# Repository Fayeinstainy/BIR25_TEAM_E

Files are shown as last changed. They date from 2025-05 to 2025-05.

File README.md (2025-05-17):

# Smart Swarmica - A Swarm Ant Robots Project
## Overview
This project is part of a biologically-inspired swarm robot system, where multiple robots cooperate to perform tasks such as locating a wireless charger and coordinating actions using IR signals.
All circuities were **initially developed and tested on a Raspberry Pi Pico**, and later **finalized on a custom PCB using RP2035 microcontroller chip** for integration into the final robot design.
The video for the whole development process and final demonstration can be found via this link: https://www.youtube.com/watch?v=agExd-AKbOk 

## Hardware Component 

- **IR LED**: IR333
- **IR Receiver**: TSOP38238
- **Microcontroller**: RP2350-based Raspberry Pi Pico 2W
  
- **Other**: Resistors, Transistors (for LED driving), 38kHz signal source (via PWM)

## System Architecture
final_robot_sys_architecture

## Power System Architecture (Normal Operation Mode)
new_robot_power_architecture

## Software Architecture
Software_algorithm drawio-2
## Motor Control
## Navigation
## Infrared Communication
- Uses **modulated IR signals** at 38kHz for one-way signaling between robots.
- Encodes simple messages (e.g. "Relative location is (4, 12)", "Stop Moving").
- Receiver uses TSOP382 to detect incoming signals reliably even in ambient light.

### How it works:
1. IR LED emits 38kHz modulated pulses.
2. TSOP382 detects signal and triggers logic in firmware.
3. Signal interpreted as communication or wall proximity.

## PCB Design
Designed using kiCAD 9.0, project files, schematic and PCB pdfs under bio_robots/ folder, featuring the following features:
- Populated: Common anode RGB LED, 3-pairs of IR transmitters and receivers, full bridge rectifier, parallel chargers for the supercapacitors, OR controller.
- Unpopulated: ICM-20948, 1.8V regulator, level shifters, bypass strategy (U12, D10-D13)

## Obstacle Avoidance
- Based on detecting reflection of IR signal from nearby obstacles.
- If TSOP382 receives the robot’s own IR pulses reflected from a wall, it triggers a "wall detected" event.
##  WI-FI Programming Mode

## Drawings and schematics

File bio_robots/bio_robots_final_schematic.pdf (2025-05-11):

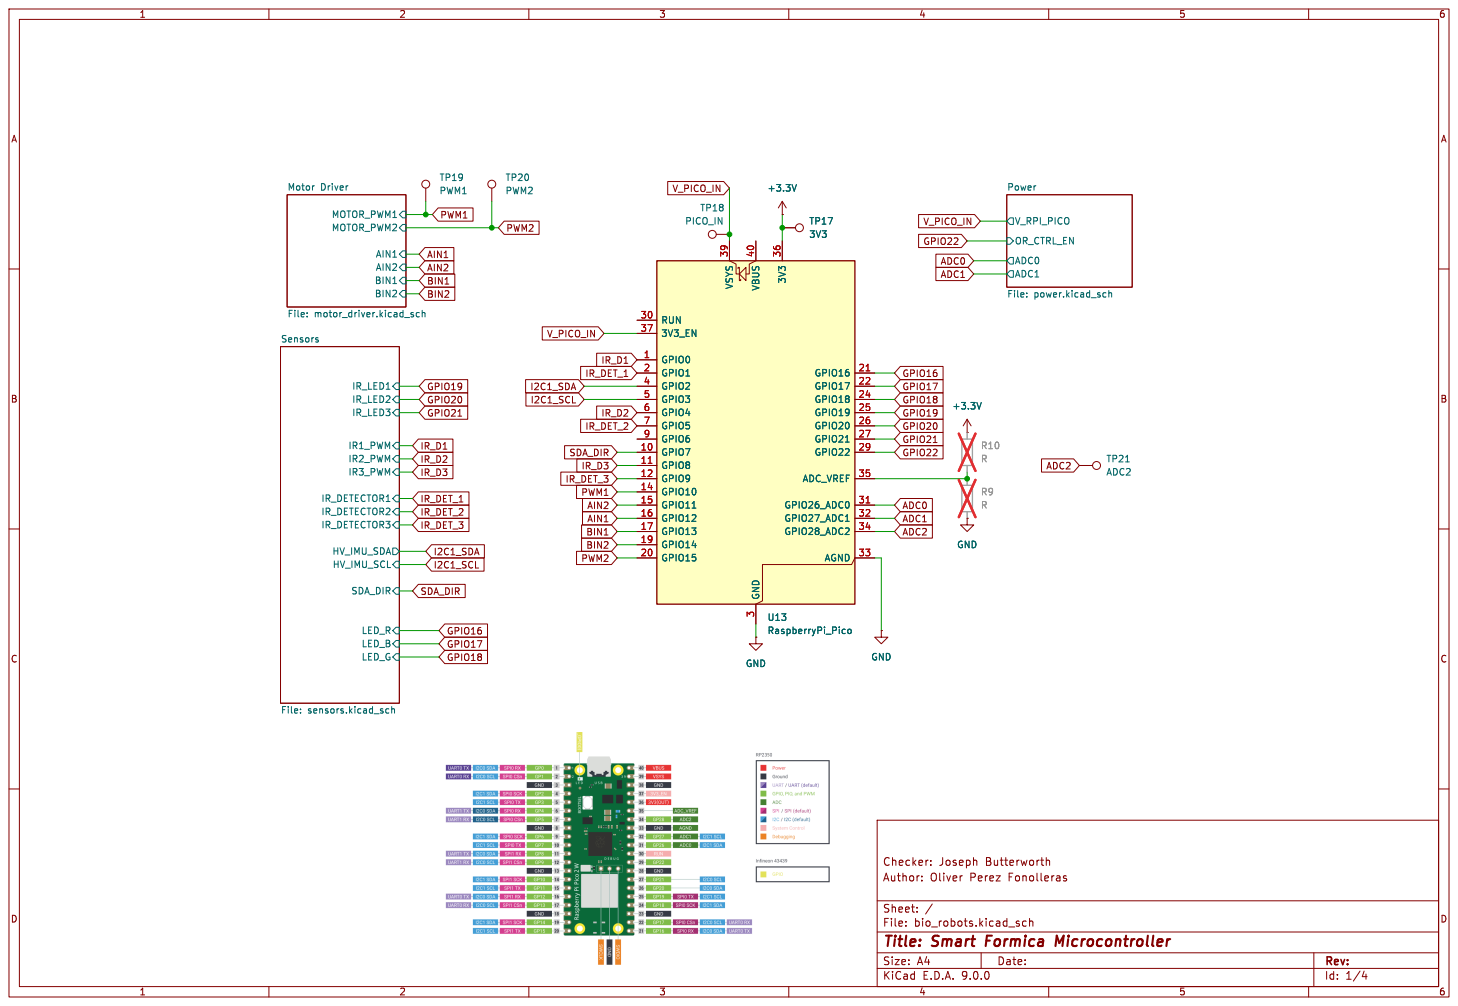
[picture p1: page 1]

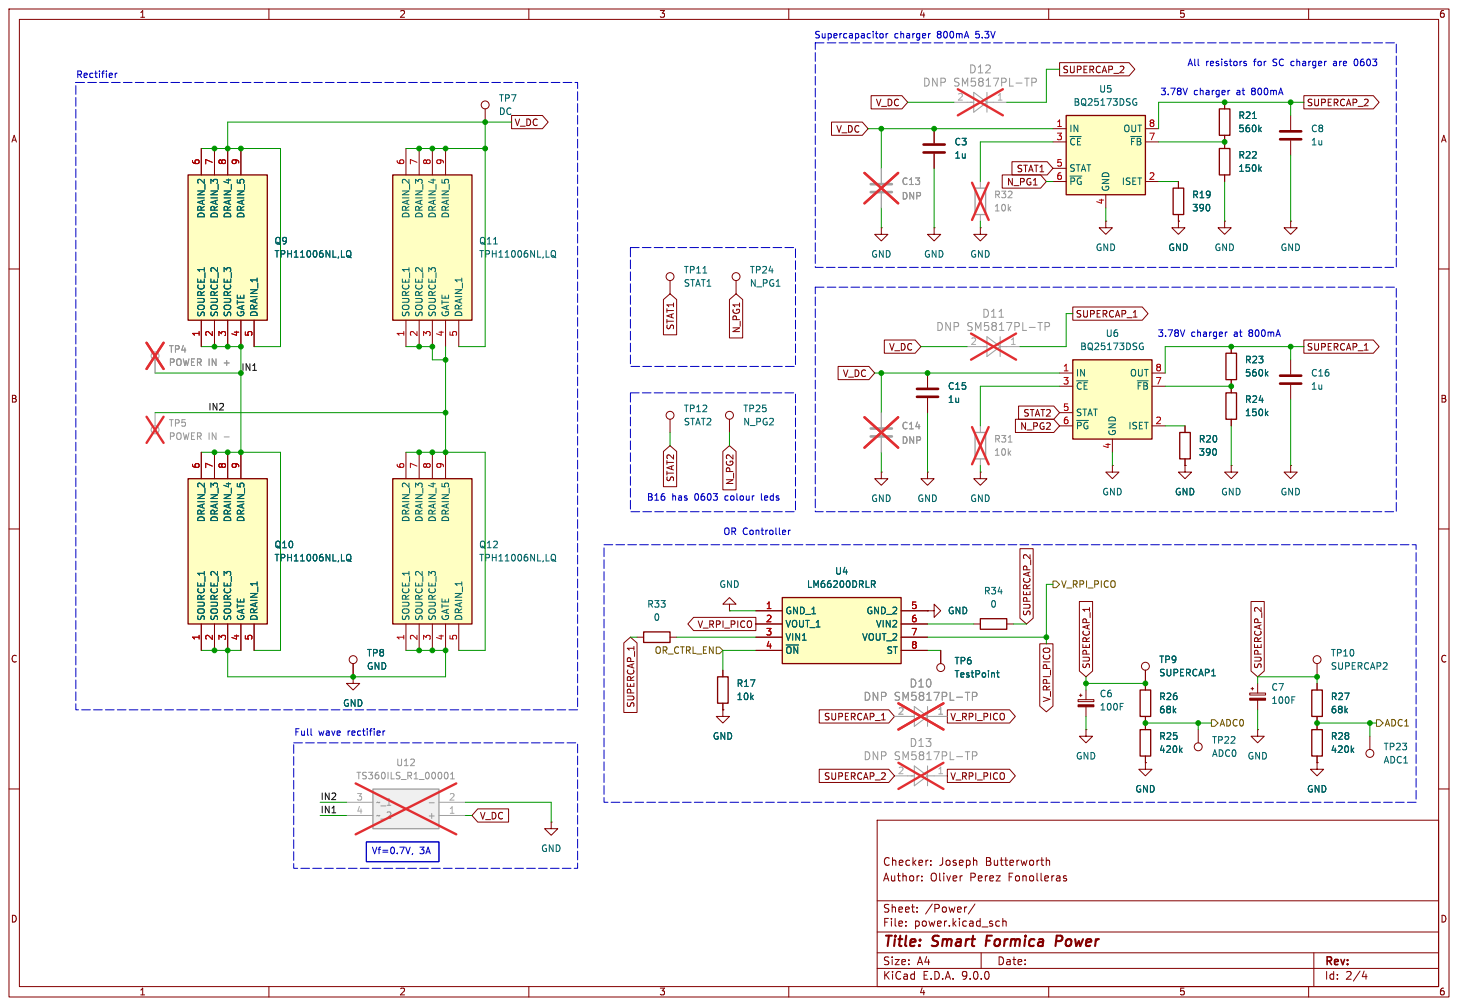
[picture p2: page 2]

6 DRAIN_3
TP5 POWER IN - TP4 POWER IN + SOURCE_1

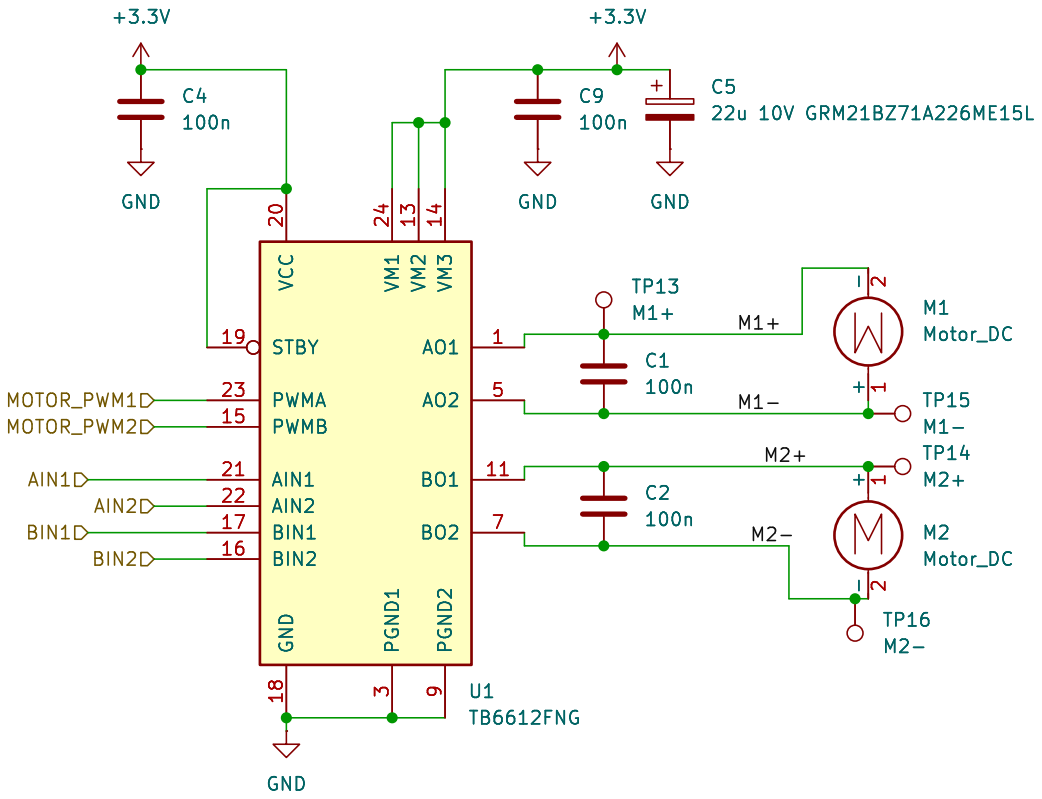
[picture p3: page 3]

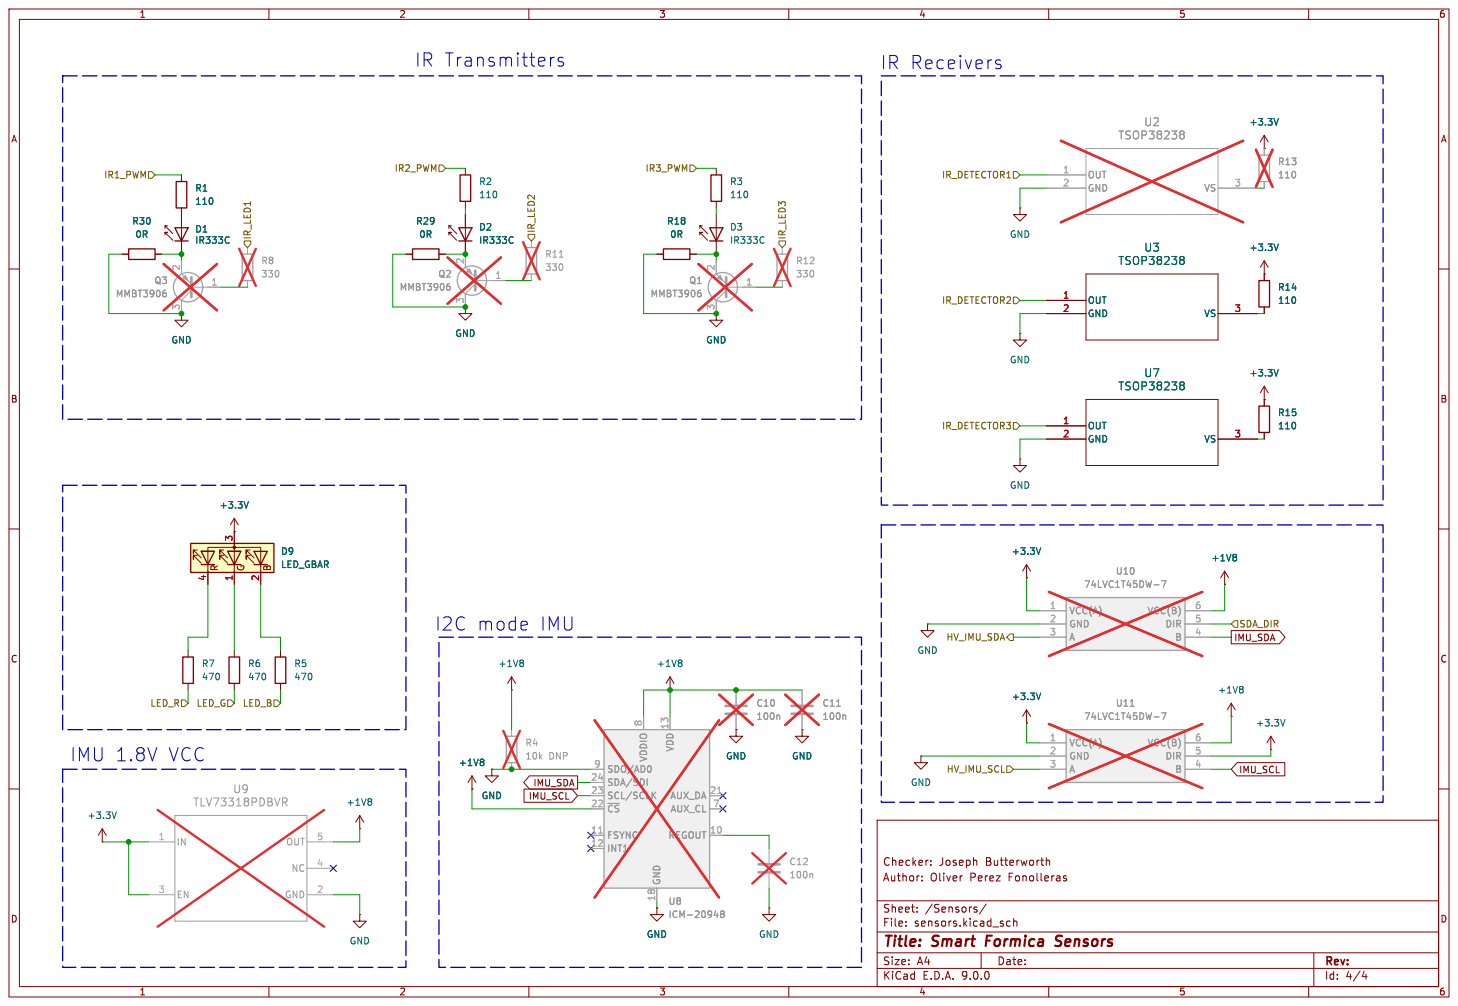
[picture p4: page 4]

Id: 4/4 Title: Smart Formica Sensors

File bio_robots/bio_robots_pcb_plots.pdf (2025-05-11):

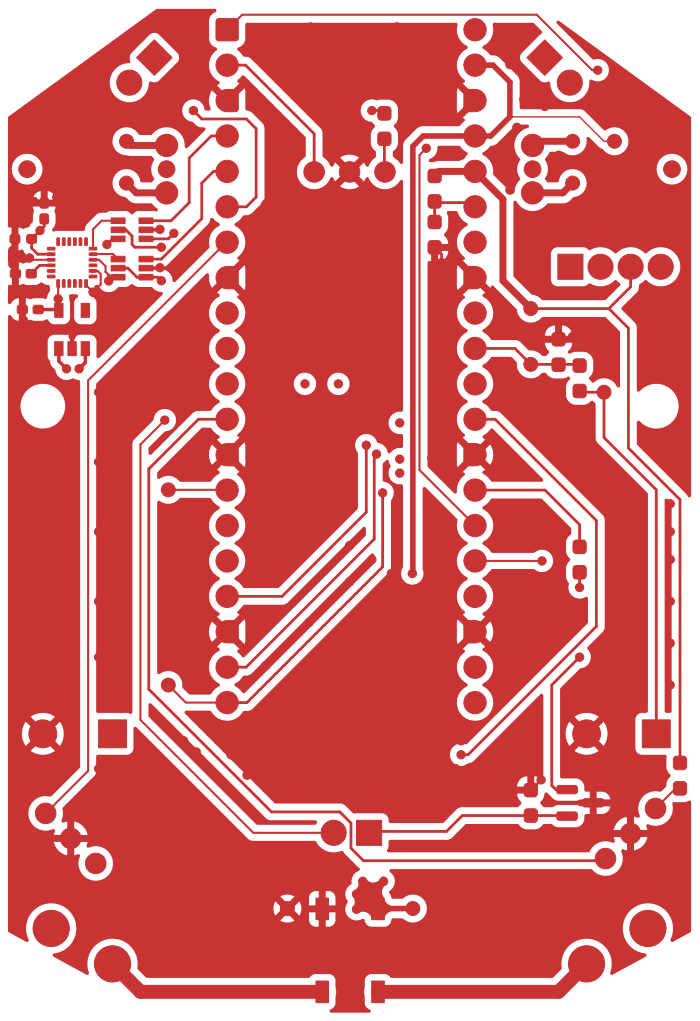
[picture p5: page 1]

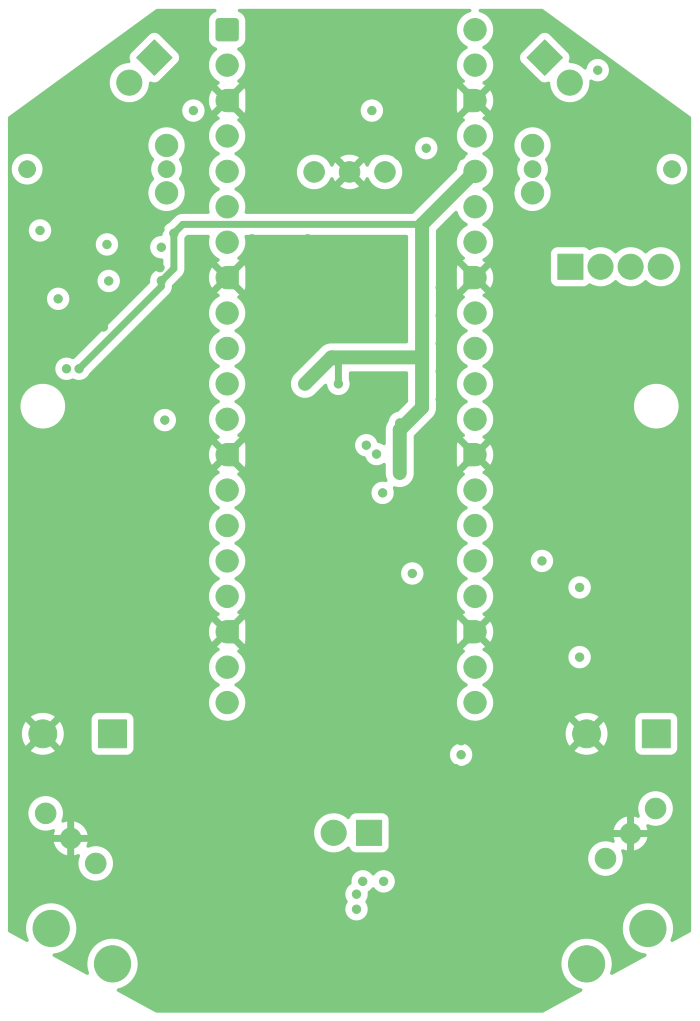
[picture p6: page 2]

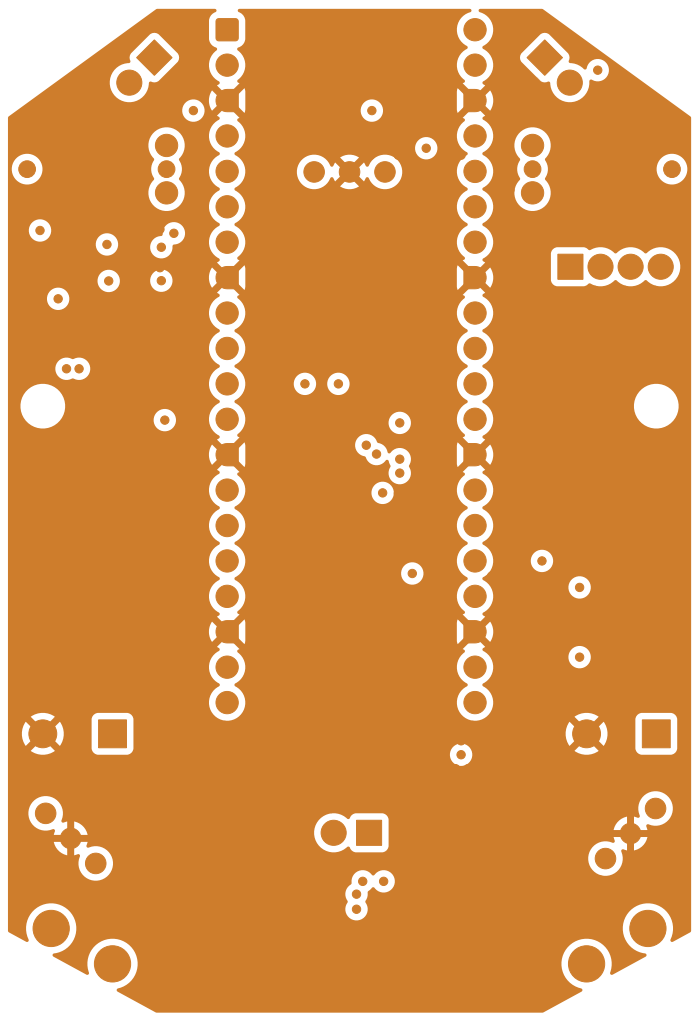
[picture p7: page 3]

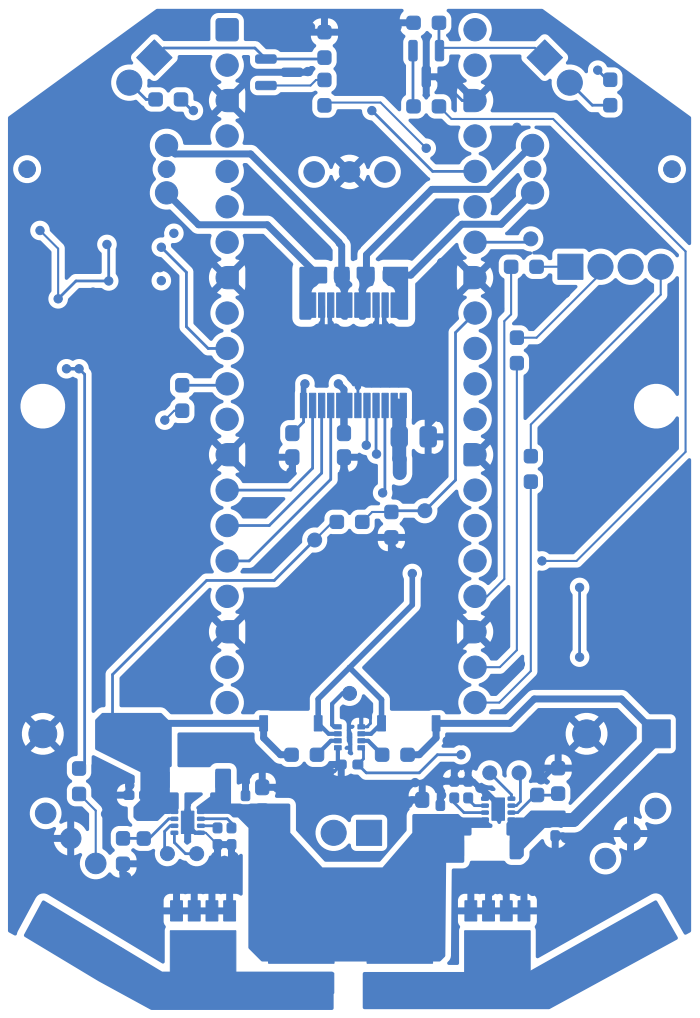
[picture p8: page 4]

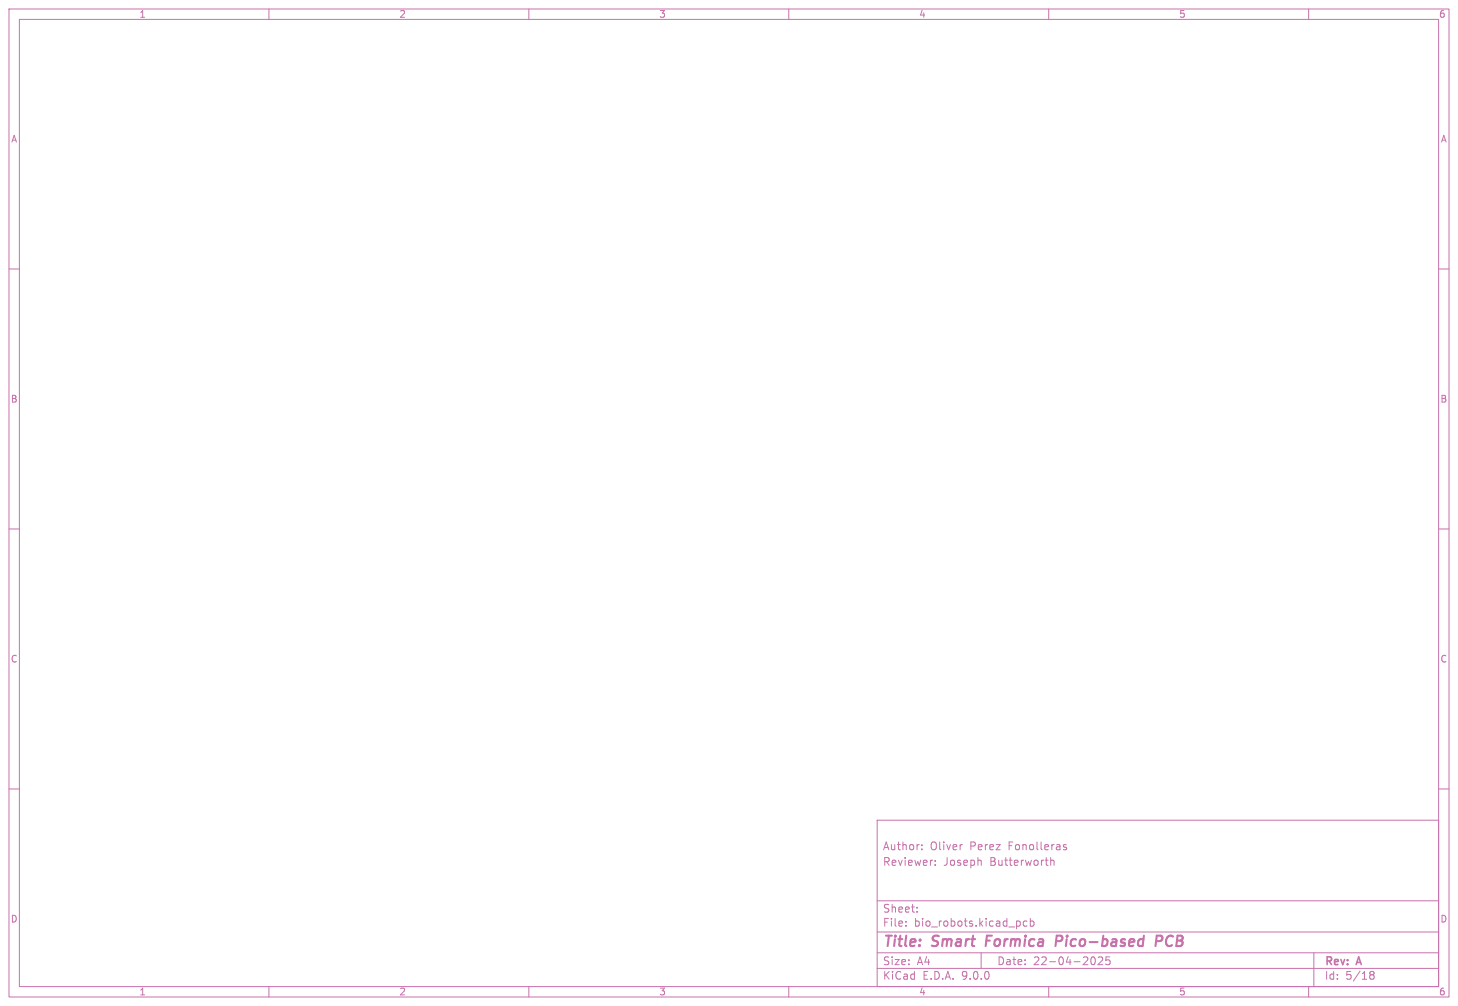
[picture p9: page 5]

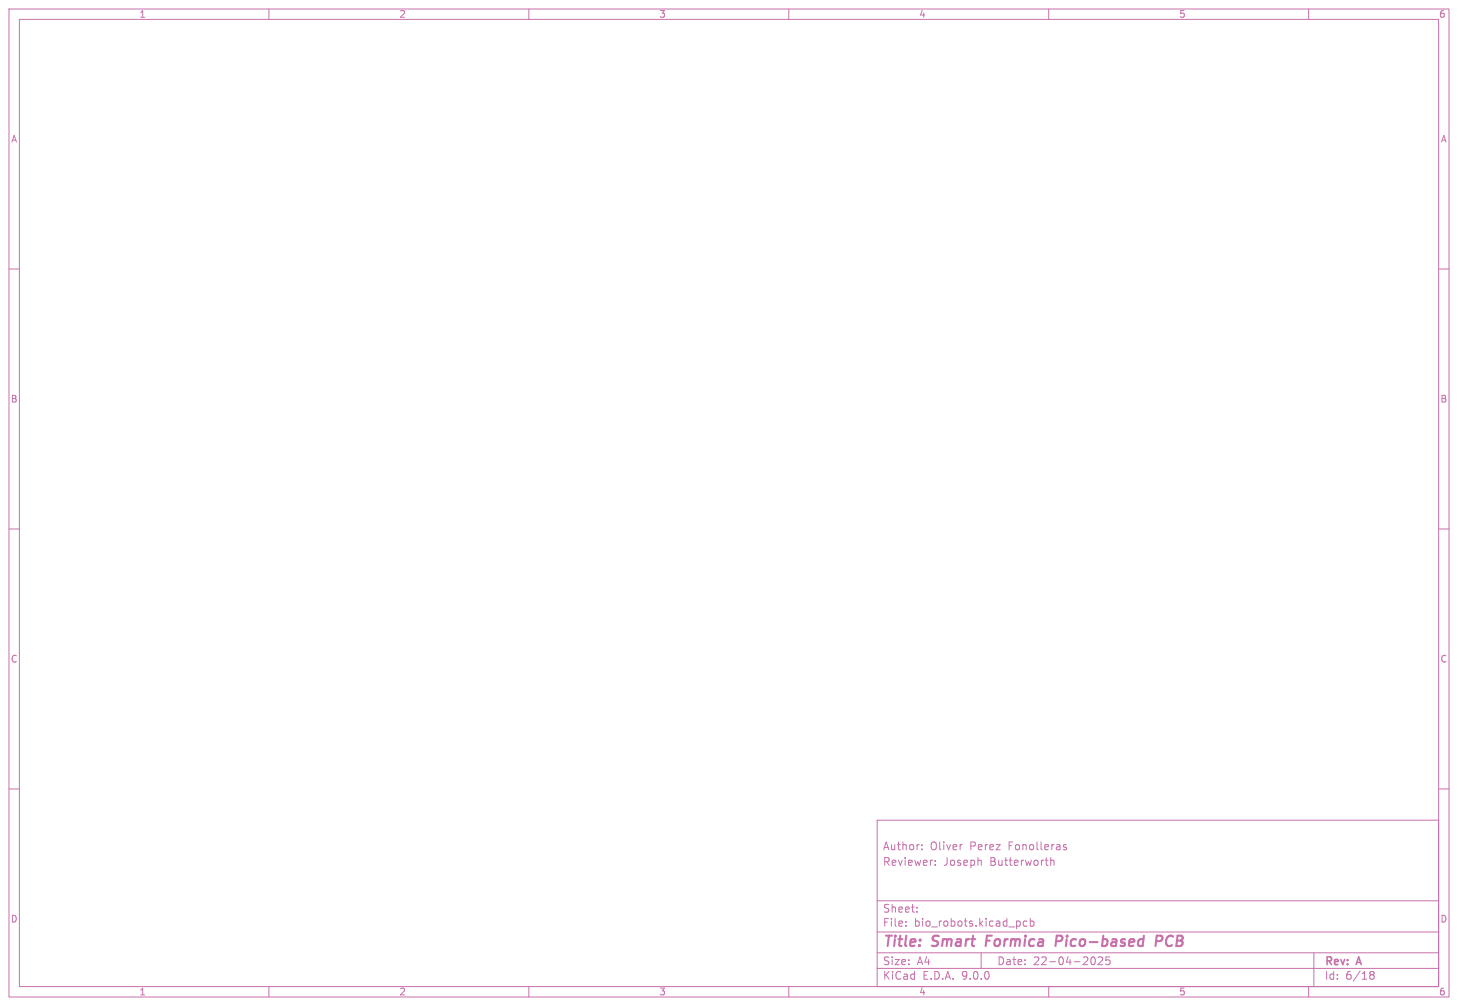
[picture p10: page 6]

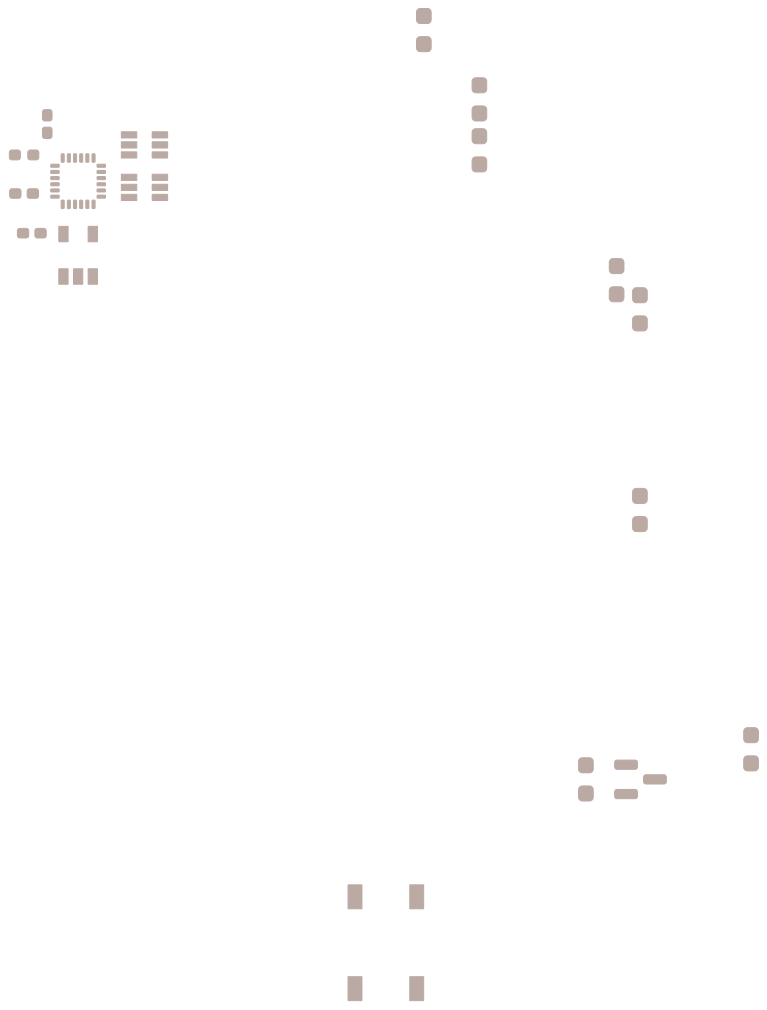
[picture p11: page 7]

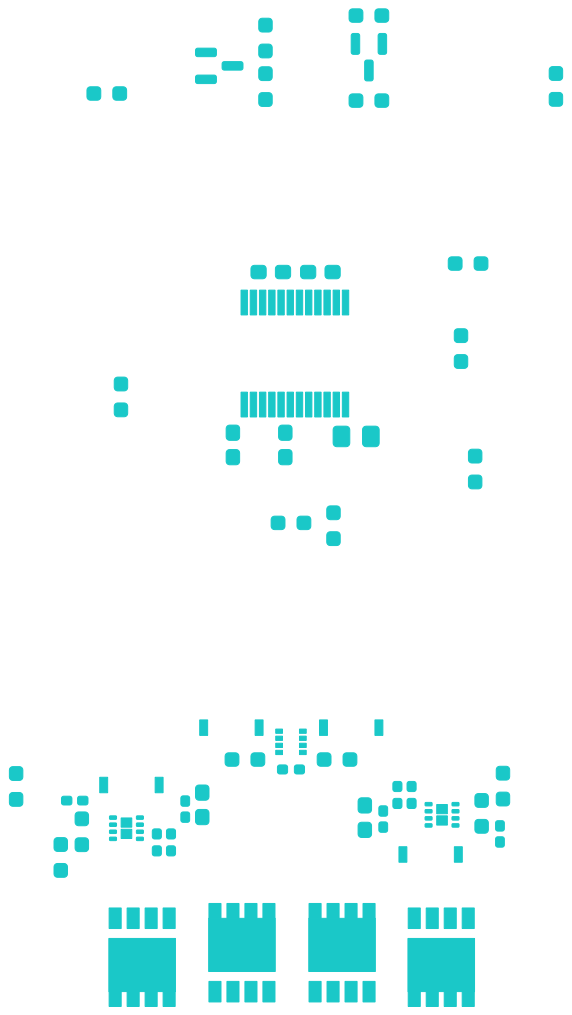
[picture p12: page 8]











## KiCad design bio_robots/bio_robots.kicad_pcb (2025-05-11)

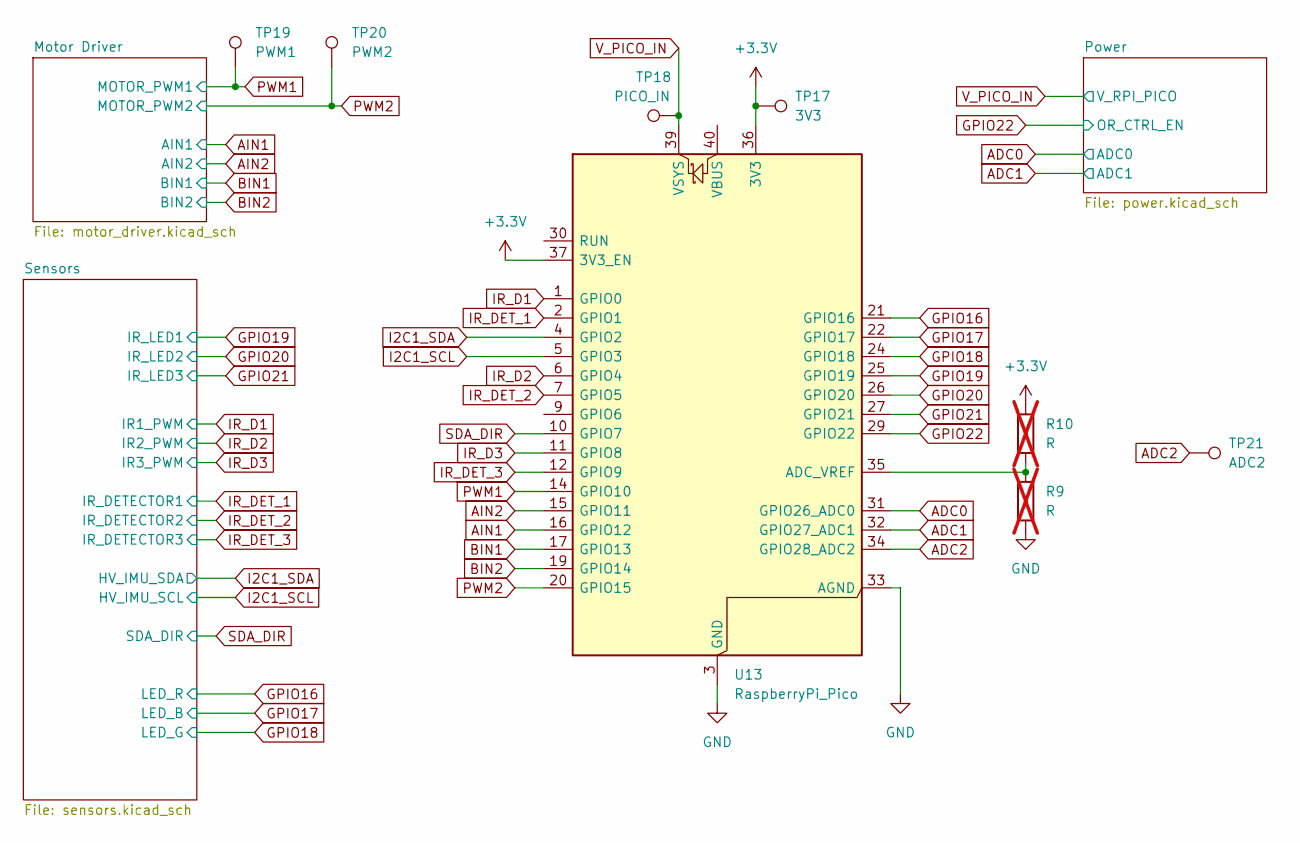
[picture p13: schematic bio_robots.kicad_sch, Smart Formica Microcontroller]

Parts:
R9, R10: R; R_0603_1608Metric_Pad0.98x0.95mm_HandSolder; not fitted
TP17: 3V3; TestPoint_Pad_D1.0mm
TP18: PICO_IN; TestPoint_Pad_D1.0mm
TP19: PWM1; TestPoint_Pad_D1.0mm
TP20: PWM2; TestPoint_Pad_D1.0mm
TP21: ADC2; TestPoint_Pad_D1.0mm
U13: RaspberryPi_Pico; mod_RaspberryPi_Pico_Common_THT

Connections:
ADC0: U13.31 (GPIO26_ADC0); also elsewhere on the board
ADC1: U13.32 (GPIO27_ADC1); also elsewhere on the board
ADC2: TP21.1, U13.34 (GPIO28_ADC2)
AIN1: U13.16 (GPIO12); also elsewhere on the board
AIN2: U13.15 (GPIO11); also elsewhere on the board
BIN1: U13.17 (GPIO13); also elsewhere on the board
BIN2: U13.19 (GPIO14); also elsewhere on the board
GND: R9.2, U13.3 (GND), U13.8 (GND), U13.13 (GND), U13.18 (GND), U13.23 (GND), U13.28 (GND), U13.33 (AGND), U13.38 (GND); also elsewhere on the board
GPIO16: U13.21 (GPIO16); also elsewhere on the board
GPIO17: U13.22 (GPIO17); also elsewhere on the board
GPIO18: U13.24 (GPIO18); also elsewhere on the board
GPIO19: U13.25 (GPIO19); also elsewhere on the board
GPIO20: U13.26 (GPIO20); also elsewhere on the board
GPIO21: U13.27 (GPIO21); also elsewhere on the board
GPIO22: U13.29 (GPIO22); also elsewhere on the board
I2C1_SCL: U13.5 (GPIO3); also elsewhere on the board
I2C1_SDA: U13.4 (GPIO2); also elsewhere on the board
IR_D1: U13.1 (GPIO0); also elsewhere on the board
IR_D2: U13.6 (GPIO4); also elsewhere on the board
IR_D3: U13.11 (GPIO8); also elsewhere on the board
IR_DET_1: U13.2 (GPIO1); also elsewhere on the board
IR_DET_2: U13.7 (GPIO5); also elsewhere on the board
IR_DET_3: U13.12 (GPIO9); also elsewhere on the board
unnamed: R9.1, R10.2, U13.35 (ADC_VREF)
PWM1: TP19.1, U13.14 (GPIO10); also elsewhere on the board
PWM2: TP20.1, U13.20 (GPIO15); also elsewhere on the board
SDA_DIR: U13.10 (GPIO7); also elsewhere on the board

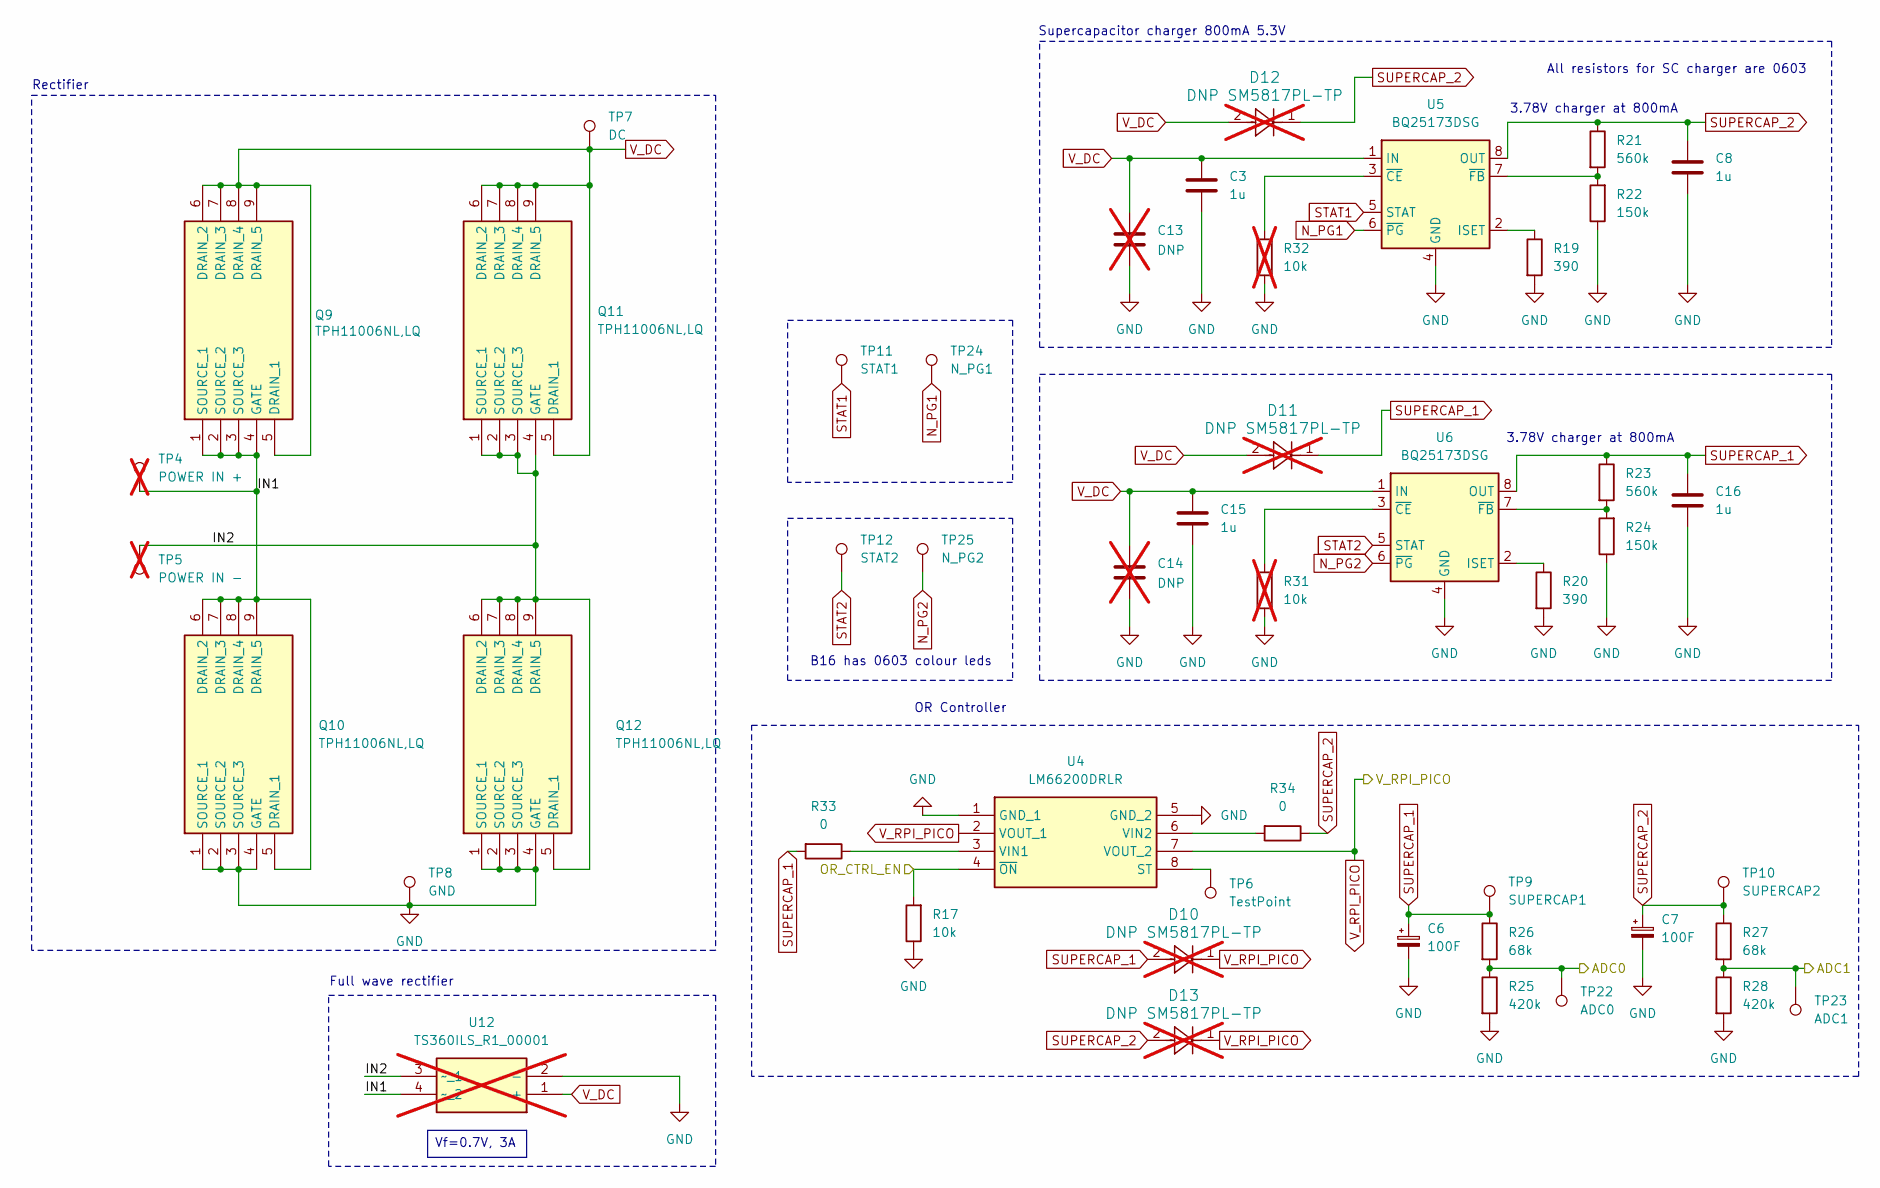
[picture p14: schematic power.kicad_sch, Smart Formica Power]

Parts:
C3, C8, C15, C16: 1u; C_0402_1005Metric_Pad0.74x0.62mm_HandSolder
C6, C7: 100F; 100f_CPhorizontal_Radial_D10.0mm_P5.00mm
C13, C14: DNP; C_0603_1608Metric_Pad1.08x0.95mm_HandSolder; not fitted
D10, D11, D12, D13: DNP SM5817PL-TP; CR_5817PL-TP_MCC-M; not fitted
Q9, Q10, Q11, Q12: TPH11006NL,LQ; TPH11006NLLQ; Mouser Part Number 757-TPH11006NLLQ
R17: 10k; R_0402_1005Metric_Pad0.72x0.64mm_HandSolder
R19, R20: 390; R_0402_1005Metric_Pad0.72x0.64mm_HandSolder
R21, R23: 560k; R_0603_1608Metric_Pad0.98x0.95mm_HandSolder
R22, R24: 150k; R_0603_1608Metric_Pad0.98x0.95mm_HandSolder
R25, R28: 420k; R_0603_1608Metric_Pad0.98x0.95mm_HandSolder
R26, R27: 68k; R_0603_1608Metric_Pad0.98x0.95mm_HandSolder
R31, R32: 10k; R_0402_1005Metric_Pad0.72x0.64mm_HandSolder; not fitted
R33, R34: 0; R_0603_1608Metric_Pad0.98x0.95mm_HandSolder
TP4: POWER IN +; TestPoint_Bridge_Pitch5.08mm_Drill1.3mm; not fitted
TP5: POWER IN -; TestPoint_Bridge_Pitch5.08mm_Drill1.3mm; not fitted
TP6: TestPoint; TestPoint_Pad_D1.0mm
TP7: DC; TestPoint_Pad_D1.0mm
TP8: GND; TestPoint_Pad_D1.0mm
TP9: SUPERCAP1; TestPoint_Pad_D1.0mm
TP10: SUPERCAP2; TestPoint_Pad_D1.0mm
TP11: STAT1; TestPoint_Pad_D1.0mm
TP12: STAT2; TestPoint_Pad_D1.0mm
TP22: ADC0; TestPoint_Pad_D1.0mm
TP23: ADC1; TestPoint_Pad_D1.0mm
TP24: N_PG1; TestPoint_Pad_D1.0mm
TP25: N_PG2; TestPoint_Pad_D1.0mm
U4: LM66200DRLR; SOTFL50P160X60-8N; Mouser Part Number 595-LM66200DRLR
U5, U6: BQ25173DSG; WSON-8-1EP_2x2mm_P0.5mm_EP0.9x1.6mm
U12: TS360ILS_R1_00001; SOP400P650X145-4N; Mouser Part Number 241-TS360ILSR100001; not fitted

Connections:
/Power/IN1: Q9.1 (SOURCE_1), Q9.2 (SOURCE_2), Q9.3 (SOURCE_3), Q9.4 (GATE), Q10.5 (DRAIN_1), Q10.6 (DRAIN_2), Q10.7 (DRAIN_3), Q10.8 (DRAIN_4), Q10.9 (DRAIN_5), TP4.1, U12.4 (~_2)
/Power/IN2: Q11.1 (SOURCE_1), Q11.2 (SOURCE_2), Q11.3 (SOURCE_3), Q11.4 (GATE), Q12.5 (DRAIN_1), Q12.6 (DRAIN_2), Q12.7 (DRAIN_3), Q12.8 (DRAIN_4), Q12.9 (DRAIN_5), TP5.1, U12.3 (~_1)
ADC0: R25.1, R26.2, TP22.1; also elsewhere on the board
ADC1: R27.2, R28.1, TP23.1; also elsewhere on the board
GND: C3.2, C6.2, C7.2, C8.2, C13.2, C14.2, C15.2, C16.2, Q10.1 (SOURCE_1), Q10.2 (SOURCE_2), Q10.3 (SOURCE_3), Q10.4 (GATE), Q12.1 (SOURCE_1), Q12.2 (SOURCE_2), Q12.3 (SOURCE_3), Q12.4 (GATE), R17.1, R19.2, R20.2, R22.1, R24.1, R25.2, R28.2, R31.1, R32.1, TP8.1, U4.1 (GND_1), U4.5 (GND_2), U5.4 (GND), U5.9 (GND), U6.4 (GND), U6.9 (GND), U12.2 (-); also elsewhere on the board
GPIO22: R17.2, U4.4 (~ON); also elsewhere on the board
N_PG1: TP24.1, U5.6 (~PG)
N_PG2: TP25.1, U6.6 (~PG)
unnamed: TP6.1, U4.8 (ST)
unnamed: R33.1, U4.3 (VIN1)
unnamed: R34.2, U4.6 (VIN2)
unnamed: R19.1, U5.2 (ISET)
unnamed: R32.2, U5.3 (~CE)
unnamed: R21.2, R22.2, U5.7 (~FB)
unnamed: R20.1, U6.2 (ISET)
unnamed: R31.2, U6.3 (~CE)
unnamed: R23.2, R24.2, U6.7 (~FB)
STAT1: TP11.1, U5.5 (STAT)
STAT2: TP12.1, U6.5 (STAT)
SUPERCAP_1: C6.1, C16.1, D10.2, D11.1, R23.1, R26.1, R33.2, TP9.1, U6.8 (OUT)
SUPERCAP_2: C7.1, C8.1, D12.1, D13.2, R21.1, R27.1, R34.1, TP10.1, U5.8 (OUT)
V_DC: C3.1, C13.1, C14.1, C15.1, D11.2, D12.2, Q9.5 (DRAIN_1), Q9.6 (DRAIN_2), Q9.7 (DRAIN_3), Q9.8 (DRAIN_4), Q9.9 (DRAIN_5), Q11.5 (DRAIN_1), Q11.6 (DRAIN_2), Q11.7 (DRAIN_3), Q11.8 (DRAIN_4), Q11.9 (DRAIN_5), TP7.1, U5.1 (IN), U6.1 (IN), U12.1 (+)

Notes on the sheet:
Rectifier
3.78V charger at 800mA
Supercapacitor charger 800mA 5.3V
OR Controller
All resistors for SC charger are 0603
B16 has 0603 colour leds
Full wave rectifier
Vf=0.7V, 3A

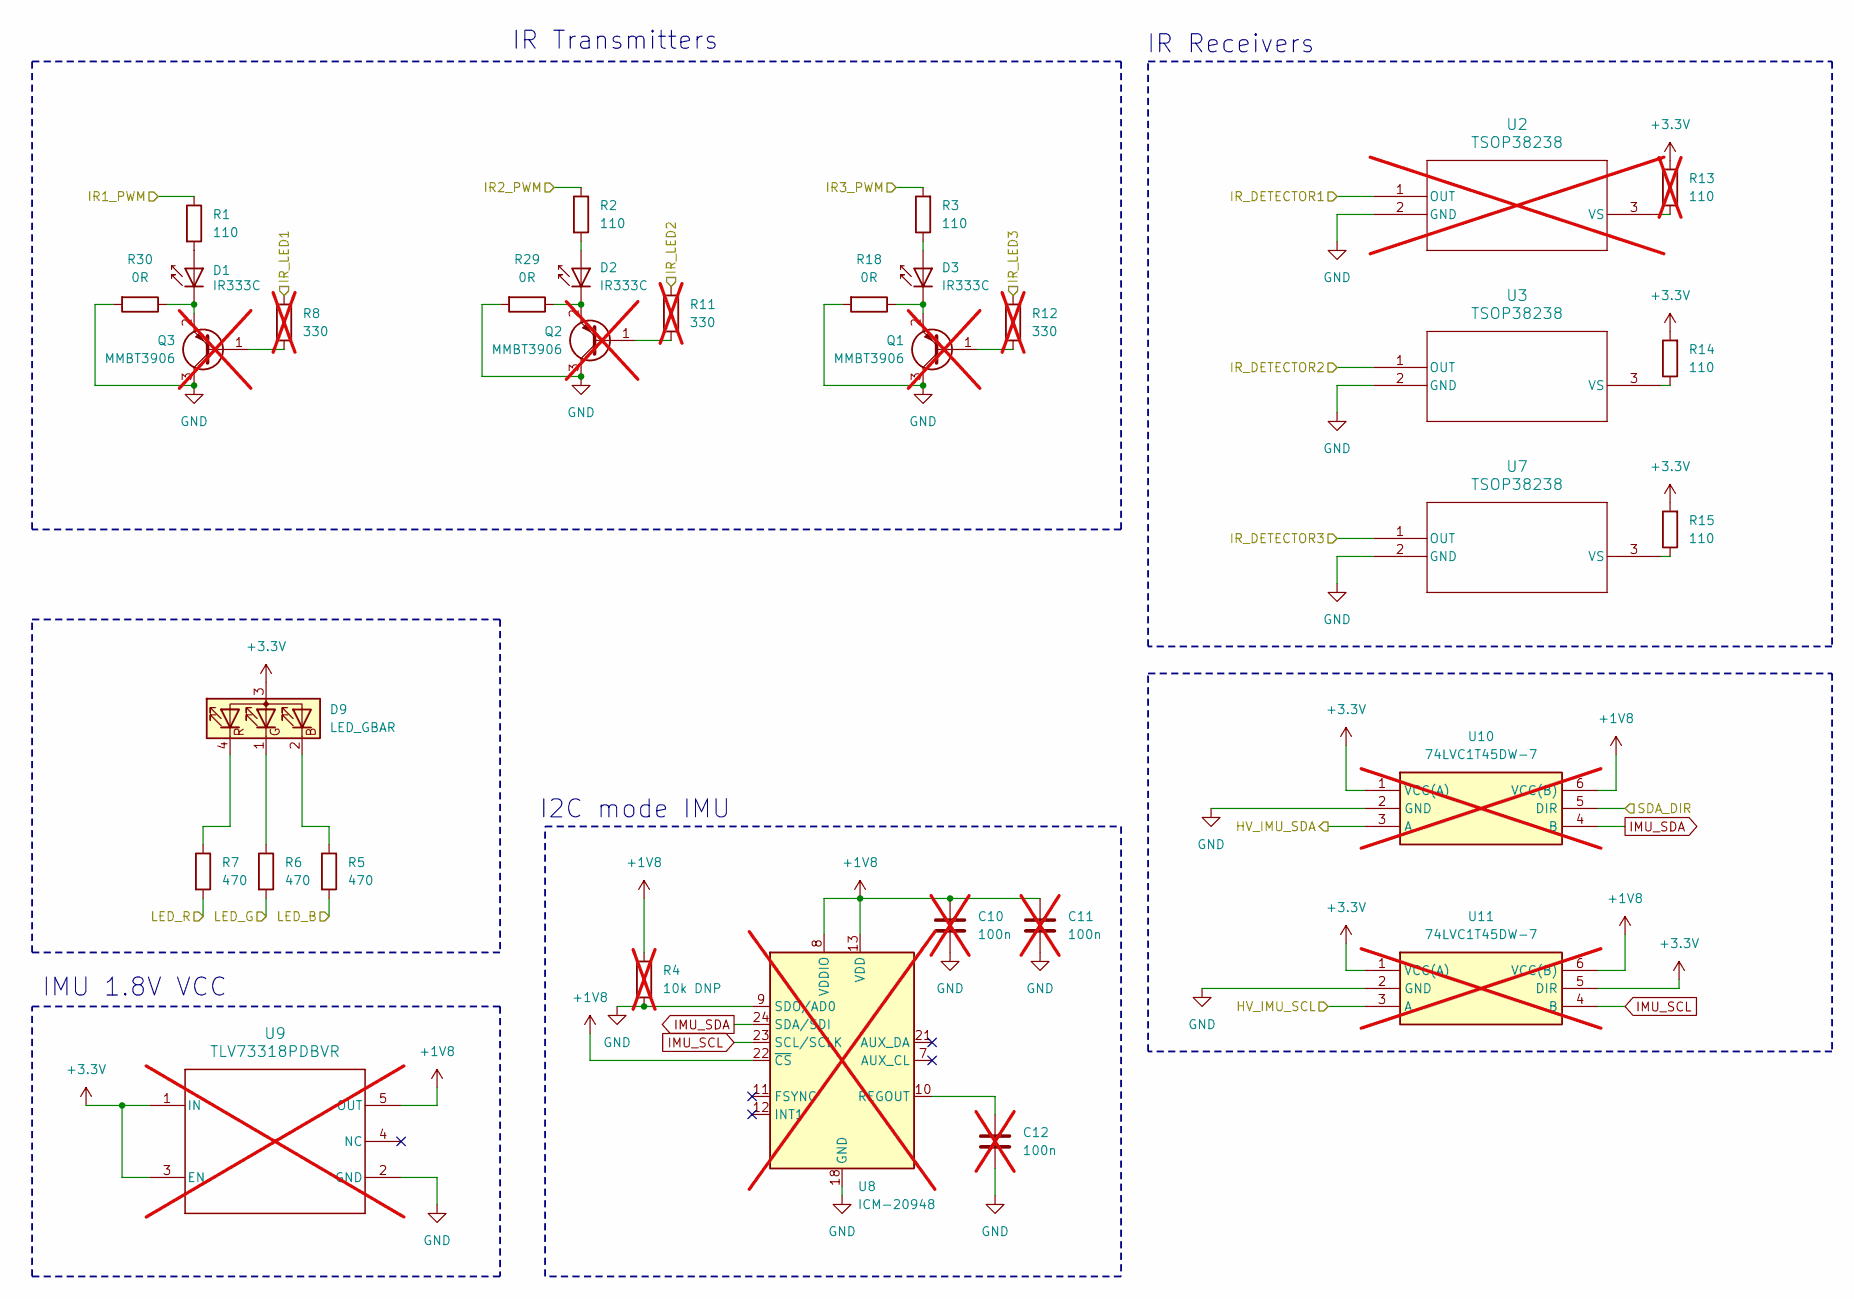
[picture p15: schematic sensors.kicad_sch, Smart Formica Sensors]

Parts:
C10, C11, C12: 100n; C_0402_1005Metric_Pad0.74x0.62mm_HandSolder; not fitted
D1, D2, D3: IR333C; LED_D5.0mm_IRGrey
D9: LED_GBAR; LED_D5.0mm-4_RGB_Wide_Pins
Q1, Q2, Q3: MMBT3906; SOT-23; not fitted
R1, R2, R3, R14, R15: 110; R_0603_1608Metric_Pad0.98x0.95mm_HandSolder
R4: 10k DNP; R_0402_1005Metric_Pad0.72x0.64mm_HandSolder; not fitted
R5, R6, R7: 470; R_0603_1608Metric_Pad0.98x0.95mm_HandSolder
R8, R11, R12: 330; R_0603_1608Metric_Pad0.98x0.95mm_HandSolder; not fitted
R13: 110; R_0603_1608Metric_Pad0.98x0.95mm_HandSolder; not fitted
R18, R29, R30: 0R; R_0603_1608Metric_Pad0.98x0.95mm_HandSolder
U2: TSOP38238; not fitted
U3, U7: TSOP38238
U8: ICM-20948; InvenSense_QFN-24_3x3mm_P0.4mm; not fitted
U9: TLV73318PDBVR; DBV0005A_N; not fitted
U10, U11: 74LVC1T45DW-7; SOT65P210X110-6N; Mouser Part Number 621-74LVC1T45DW-7; not fitted

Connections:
+1V8: C10.1, C11.1, R4.1, U8.8 (VDDIO), U8.13 (VDD), U8.22 (~CS), U9.5 (OUT), U10.6 (VCC(B)), U11.6 (VCC(B))
GND: C10.2, C11.2, C12.2, Q1.3 (C), Q2.3 (C), Q3.3 (C), R4.2, R18.2, R29.2, R30.2, U2.2 (GND), U3.2 (GND), U7.2 (GND), U8.9 (SDO/AD0), U8.18 (GND), U8.20 (GND), U9.2 (GND), U10.2 (GND), U11.2 (GND); also elsewhere on the board
GPIO16: R7.2; also elsewhere on the board
GPIO17: R5.2; also elsewhere on the board
GPIO18: R6.2; also elsewhere on the board
GPIO19: R8.1; also elsewhere on the board
GPIO20: R11.1; also elsewhere on the board
GPIO21: R12.1; also elsewhere on the board
I2C1_SCL: U11.3 (A); also elsewhere on the board
I2C1_SDA: U10.3 (A); also elsewhere on the board
IMU_SCL: U8.23 (SCL/SCLK), U11.4 (B)
IMU_SDA: U8.24 (SDA/SDI), U10.4 (B)
IR_D1: R1.1; also elsewhere on the board
IR_D2: R2.1; also elsewhere on the board
IR_D3: R3.2; also elsewhere on the board
IR_DET_1: U2.1 (OUT); also elsewhere on the board
IR_DET_2: U3.1 (OUT); also elsewhere on the board
IR_DET_3: U7.1 (OUT); also elsewhere on the board
unnamed: D1.2 (A), R1.2
unnamed: D1.1 (K), Q3.2 (E), R30.1
unnamed: D2.2 (A), R2.2
unnamed: D2.1 (K), Q2.2 (E), R29.1
unnamed: D3.2 (A), R3.1
unnamed: D3.1 (K), Q1.2 (E), R18.1
unnamed: D9.2 (BK), R5.1
unnamed: D9.1 (GK), R6.1
unnamed: D9.4 (RK), R7.1
unnamed: Q1.1 (B), R12.2
unnamed: Q2.1 (B), R11.2
unnamed: Q3.1 (B), R8.2
unnamed: R13.1, U2.3 (VS)
unnamed: R14.1, U3.3 (VS)
unnamed: R15.1, U7.3 (VS)
unnamed: C12.1, U8.10 (REGOUT)
SDA_DIR: U10.5 (DIR); also elsewhere on the board

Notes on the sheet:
IR Receivers
IR Transmitters
I2C mode IMU
IMU 1.8V VCC

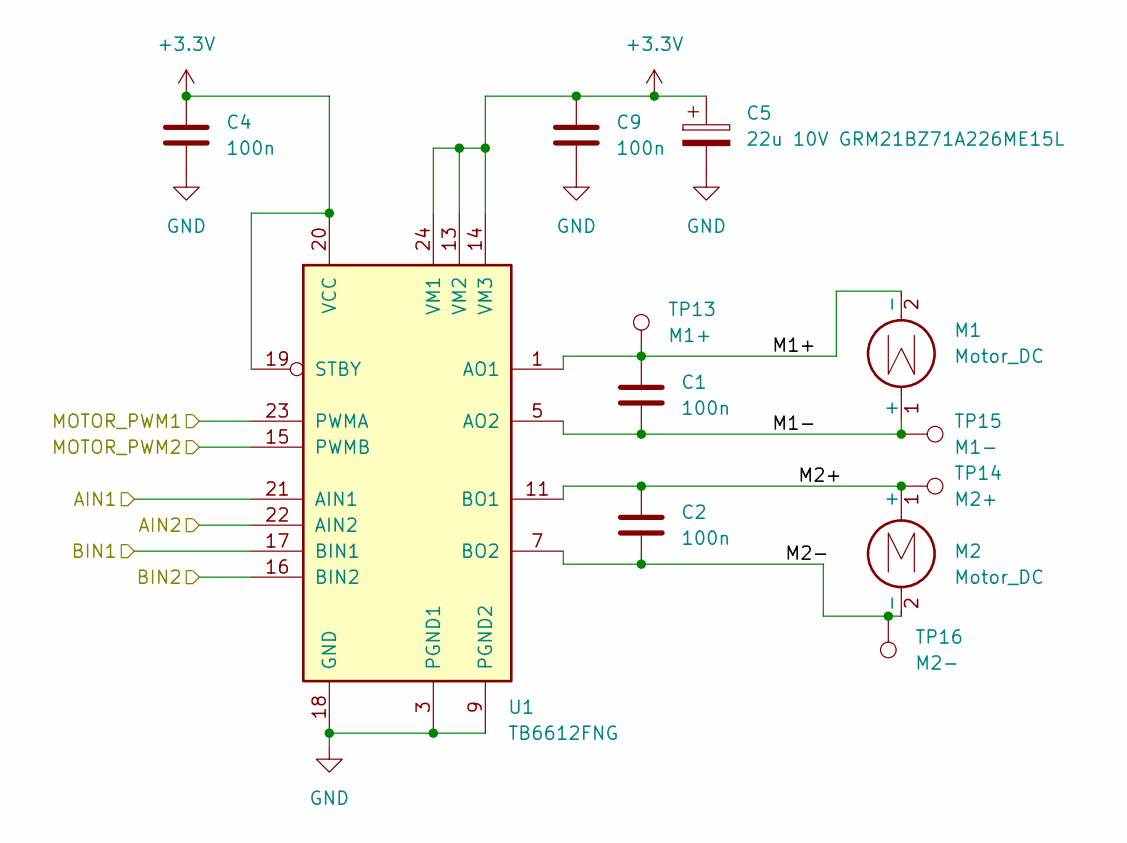
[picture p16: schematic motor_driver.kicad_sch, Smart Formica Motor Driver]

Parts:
C1, C2, C4, C9: 100n; C_0603_1608Metric_Pad1.08x0.95mm_HandSolder
C5: 22u 10V GRM21BZ71A226ME15L; C_0805_2012Metric_Pad1.18x1.45mm_HandSolder
M1, M2: Motor_DC; mod_motor_v2_VZ6SC0B0060081
TP13: M1+; TestPoint_Pad_D1.0mm
TP14: M2+; TestPoint_Pad_D1.0mm
TP15: M1-; TestPoint_Pad_D1.0mm
TP16: M2-; TestPoint_Pad_D1.0mm
U1: TB6612FNG; SSOP-24_5.3x8.2mm_P0.65mm

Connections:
/Motor Driver/M1+: C1.1, M1.2 (-), TP13.1, U1.1 (AO1), U1.2 (AO1)
/Motor Driver/M1-: C1.2, M1.1 (+), TP15.1, U1.5 (AO2), U1.6 (AO2)
/Motor Driver/M2+: C2.1, M2.1 (+), TP14.1, U1.11 (BO1), U1.12 (BO1)
/Motor Driver/M2-: C2.2, M2.2 (-), TP16.1, U1.7 (BO2), U1.8 (BO2)
AIN1: U1.21 (AIN1); also elsewhere on the board
AIN2: U1.22 (AIN2); also elsewhere on the board
BIN1: U1.17 (BIN1); also elsewhere on the board
BIN2: U1.16 (BIN2); also elsewhere on the board
GND: C4.2, C5.2, C9.2, U1.3 (PGND1), U1.4 (PGND1), U1.9 (PGND2), U1.10 (PGND2), U1.18 (GND); also elsewhere on the board
PWM1: U1.23 (PWMA); also elsewhere on the board
PWM2: U1.15 (PWMB); also elsewhere on the board

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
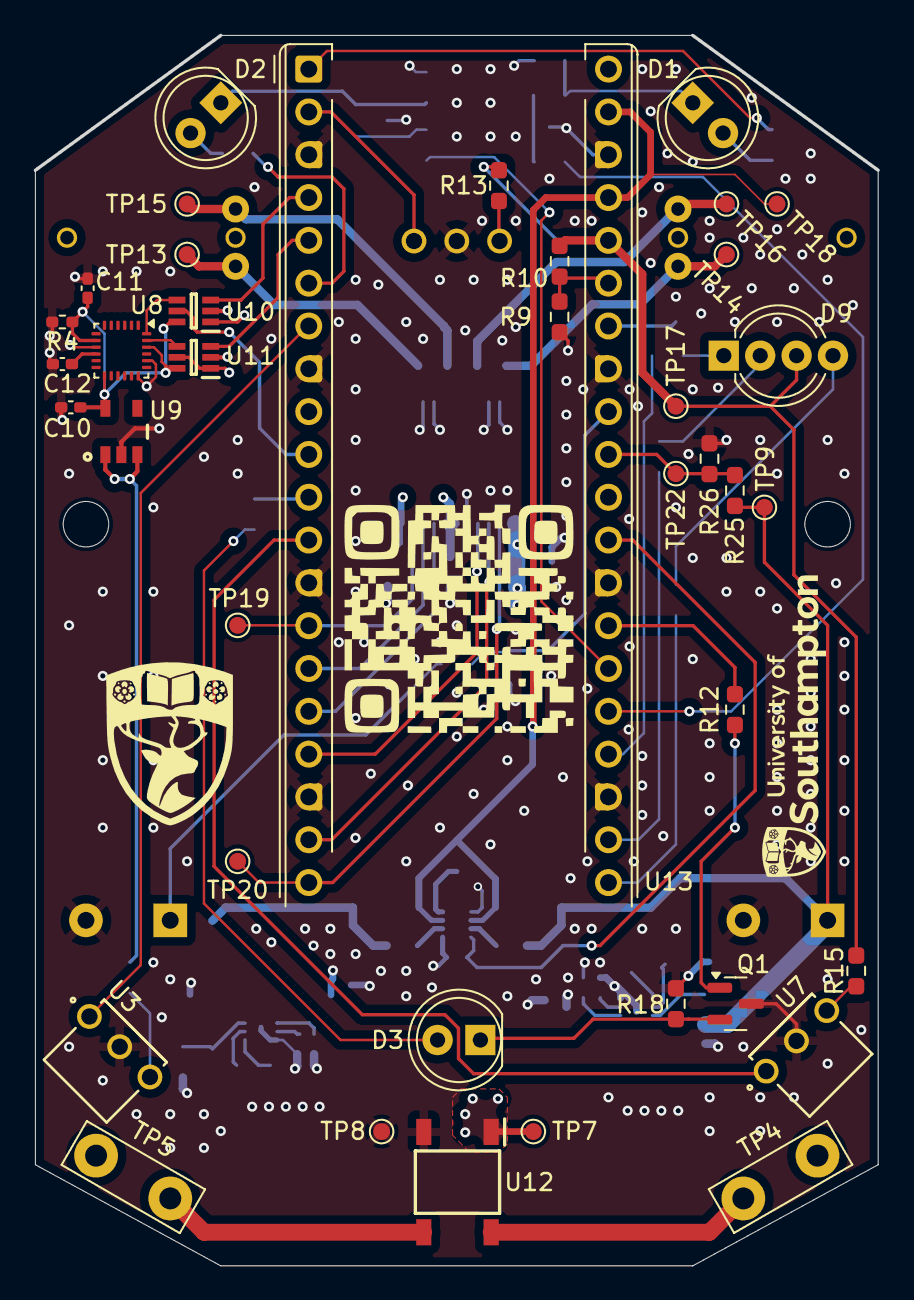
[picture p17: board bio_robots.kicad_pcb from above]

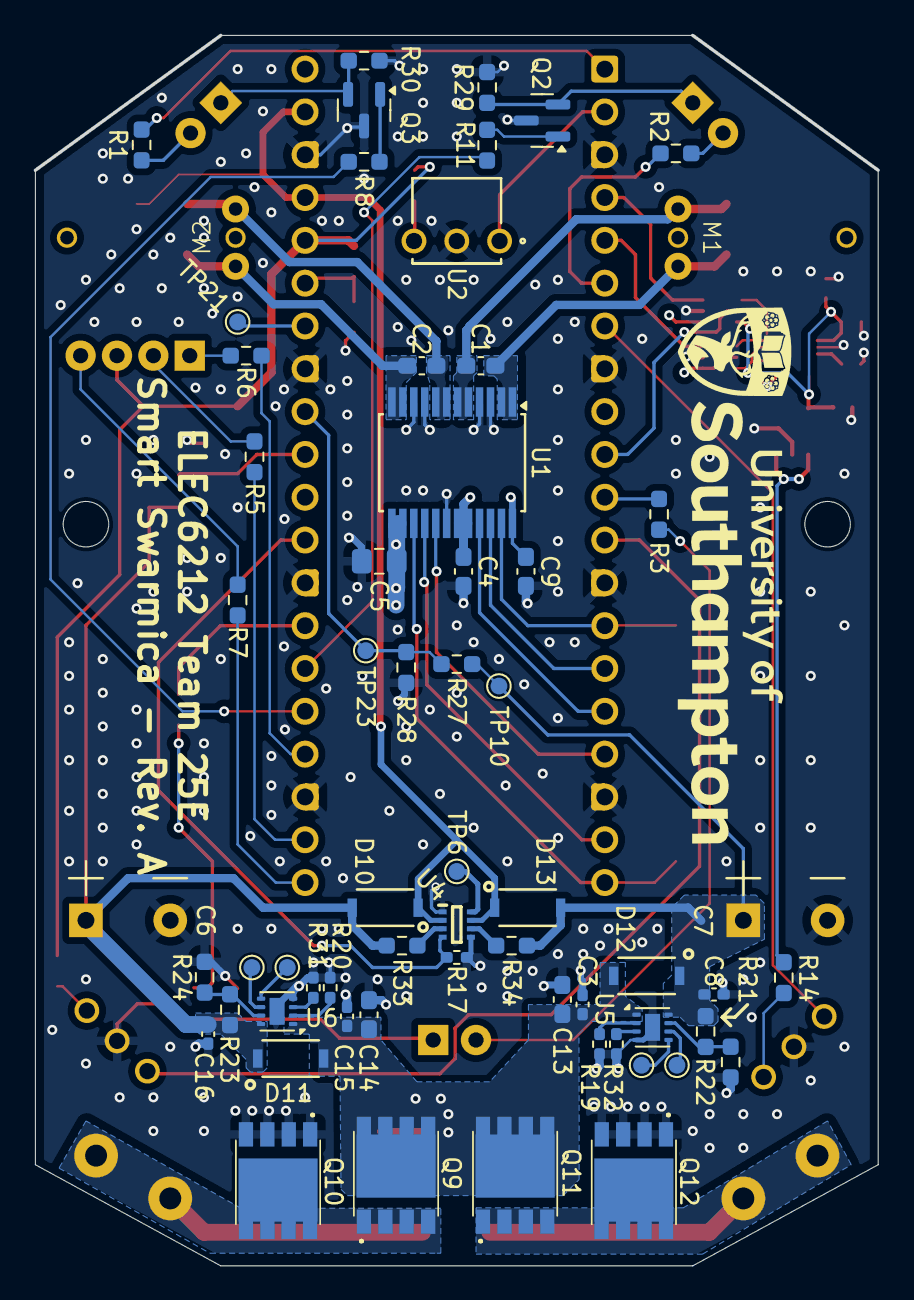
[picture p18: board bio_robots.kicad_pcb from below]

Board: 4 copper layers, 50.0 x 73.0 mm, 103 parts (62 on the bottom side), 70 nets.

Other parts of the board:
MH1, MH2: MountingHole_2.7mm_M2.5_DIN965

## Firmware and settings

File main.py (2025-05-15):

from picozero import RGBLED
from time import sleep
import math
import random
from machine import Pin , PWM
import machine
import rp2
import sys
import time
#from machine import WDT, reset
from machine import reset, WDT, Pin, PWM, reset_cause, PWRON_RESET

# if machine.reset_cause() != machine.PWRON_RESET:  # 如果不是上电复位
#     print("wrong detecting, resetting...")
#     time.sleep(1)       # 等待串口输出完成
#     machine.reset()     # 强制硬件复位

wdt = WDT(timeout=8000) #8 seconds watchdog

# --------- Setup --------- #
IR_transmitter_pin = PWM(Pin(0))
IR_transmitter_pin.freq(38000)  # 38kHz carrier
IR_transmitter_pin2 = PWM(Pin(4))
IR_transmitter_pin2.freq(38000)  # 38kHz carrier
IR_transmitter_pin3 = PWM(Pin(8))
IR_transmitter_pin3.freq(38000)  # 38kHz carrier

IR_receiver_pin1 = Pin(5, Pin.IN)
IR_receiver_pin2 = Pin(9, Pin.IN)
#1 and 9 are not working on Beth.(No Rx 1)
#1 not working on Bella (No Rx 1)
#1 not working on Cursed (No Rx 1)

rgb = RGBLED(red = 16, green = 17, blue = 18,active_high=False)

IR_transmitter_pin.duty_u16(38000)  # Enable IR signal
IR_transmitter_pin2.duty_u16(38000)  # Enable IR signal
IR_transmitter_pin3.duty_u16(38000)  # Enable IR signal

# tran1 = Pin(19, Pin.OUT)
# tran2 = Pin(20, Pin.OUT)
# tran3 = Pin(21, Pin.OUT)
# 
# tran1.value(0)
# tran2.value(0)
# tran3.value(0)
#detected = False
#--------------------walldetection----------#
def wall_detection_notworking():
    print("Wall detection started")
    #IR_transmitter_pin.duty_u16(32768)
    start = time.ticks_ms()
    
    
    while time.ticks_diff(time.ticks_ms(),start) < WALL_DETECTION_WINDOW_MS:
        if IR_receiver_pin.value()==0:
            #print("IR Signal Detected!")
            detected = True
        #elif IR_receiver_pin.value()==0:
            #print("No Signal")
    
    #IR_transmitter_pin.duty_u16(0)
    if detected == True:
        print("Wall detected")
        rgb.color = (255,0,0) #red
        sleep(1)
        #led_receiver_pin.value(1)

    else:
        print("Wall cleared!")
        rgb.color =(100,0,100) #red+green
        sleep(1)
        #led_receiver_pin.value(0)
        
# --------- Wall Detection --------- #
def wall_detection():
     
    #print("Wall detection started")
    #global detected

    time.sleep_ms(1)  # Allow some time for signal to bounce back

    if IR_receiver_pin1.value()==0 or IR_receiver_pin2.value() == 0:
        #detected = True
        print("IR Signal Detected!")
        rgb.color = (255, 0, 0) #red
        return True
    else:
        print("No Signal.")
        rgb.color = (0, 0, 255) #
        return False

#---------------------motor/navigation--------------------
#rgb = RGBLED(red = 16, green = 17, blue = 18,active_high=False) 
distance = 1.0 #polar distancce of the current location
angle = 0.0 #polar angle of the current location
direction = 0.0 #where the robot is facing
coord = [distance,angle, direction] 
turn_left = 0
turn_right = 0
turn = [turn_left, turn_right] 
count = 0
led = Pin('LED', Pin.OUT)

ain1 = Pin(12,Pin.OUT)
ain2 = Pin(11, Pin.OUT)
bin1 = Pin(13,Pin.OUT)
bin2 = Pin(14,Pin.OUT)
pwma = PWM(Pin(10))
pwmb = PWM(Pin(15))
pwma.freq(24000)
pwmb.freq(24000)

def RotateCW(duty, pwm):
    ain1.value(1)
    ain2.value(0)
    bin1.value(1)
    bin2.value(0)
    duty_16 = int(duty)
    pwm.duty_u16(duty_16)

def RotateCCW(duty, pwm):
    ain1.value(0)
    ain2.value(1)
    bin1.value(0)
    bin2.value(1)
    duty_16 = int(duty)
    pwm.duty_u16(duty_16)
    led.toggle()
    
def StopMotor():

    pwma.duty_u16(0)
    pwmb.duty_u16(0)
    led.toggle()
    
def forward(duty):
    x = coord[0]*math.cos(coord[1]) + math.cos(coord[2])
    y = coord[0]*math.sin(coord[1]) + math.sin(coord[2])
    coord[0] = math.sqrt(x**2 + y**2)
    coord[1] = math.atan2(y,x)
    RotateCW(duty, pwma)
    RotateCW(duty, pwmb)
    rgb.color = (255, 0, 0) #red

    return coord,turn

def leftback(duty):
    coord[2] += math.pi/2
    coord[2] = (coord[2] + math.pi) % (2 * math.pi) - math.pi  # Keep within [-π, π]

    x = coord[0]*math.cos(coord[1]) + math.cos(coord[2])
    y = coord[0]*math.sin(coord[1]) + math.sin(coord[2])
    coord[0] = math.sqrt(x**2 + y**2)
    coord[1] = math.atan2(y,x)
    turn[0] +=1
    rgb.color = (0, 255, 0) #blue
    RotateCCW(duty, pwma)
    RotateCW(duty/1.2, pwmb)
    return coord,turn

def rightback(duty):
    coord[2] -= math.pi/2
    coord[2] = (coord[2] + math.pi) % (2 * math.pi) - math.pi  # Keep within [-π, π]

    x = coord[0]*math.cos(coord[1]) + math.cos(coord[2])
    y = coord[0]*math.sin(coord[1]) + math.sin(coord[2])
    coord[0] = math.sqrt(x**2 + y**2)
    coord[1] = math.atan2(y,x)
    turn[1] += 1
    rgb.color = (0, 0, 255) #green
    RotateCW(duty/1.2, pwma)
    RotateCCW(duty, pwmb)
    return coord,turn


def backward(duty):
    x = coord[0]*math.cos(coord[1]) - math.cos(coord[2])
    y = coord[0]*math.sin(coord[1]) - math.sin(coord[2])
    coord[0] = math.sqrt(x**2 + y**2)
    coord[1] = math.atan2(y,x)
    rgb.color = (255, 128, 0) #orange
    RotateCCW(duty, pwma)
    RotateCCW(duty, pwmb)

    return coord,turn

def foraging():
    '''Randomly move to find a charger'''
    count = 0
    while (math.fabs(coord[0]*math.cos(coord[1]) - station[0]*math.cos(station[1])) > 2 or math.fabs(coord[0]*math.sin(coord[1]) - station[0]*math.sin(station[1])) > 2)  and count < 30:
        random.choice(movement)(48000)
        sleep(3)
        print(coord,turn)
        count +=1
        rgb.color= (0,0,0)
        sleep(1)
        #if math.fabs(coord[0] - station[0]) < 1 and math.cos(coord[1]) * math.cos(station[1]) > 0 and math.sin(coord[1]) * math.sin(station[1]) > 0:
           # print('Gettng there')   these are for debugging purpose 
    return coord
#stop and talk to each other
def get_charge(destination):
    """Navigates the robot to the charger"""
    count = 0
    while math.fabs(coord[0]*math.sin(coord[1]) - destination[1]) > 0.9 and count < 100 :
        if  coord[0]*math.sin(coord[1]) <= destination[1] : # Robot needs to move up
            if not (math.pi/2 -0.2 < coord[2] < math.pi/2 +0.2):
                left()
                sleep(0.5)
            else:
                forward()
                sleep(0.5)
        else: #robot needs to move down
            if not ( -math.pi/2 - 0.2 <coord[2] < -math.pi/2 + 0.2):  # Check if robot is facing down
                right()  # Turn right to face downward
                sleep(0.5)
            else:
                forward()  # Move forward
                sleep(0.5)
        print(coord[0]*math.sin(coord[1]))
        count +=1
    while math.fabs(coord[0]*math.cos(coord[1]) - destination[0]) > 0.9 and count < 100 :
        if  coord[0]*math.cos(coord[1]) > destination[0]: # Move to the left
            if (-math.pi/2-0.000001 <= coord[2] <= math.pi/2):  # Check if robot is facing left
                left()  # Turn left to face right
                sleep(0.5)
            else:
                forward()  # Move forward
                sleep(0.5)
        else:  # Need to go towards positive X direction
            if not (-0.2 <coord[2] < 0.2) :  # Check if robot is facing right
                right()  # Turn right to face left
                sleep(0.5)
            else:
                forward()  # Move forward
                sleep(0.5)
        print(coord[0]*math.cos(coord[1]))
        count +=1
    print(coord)
    return coord

def main():
    start_time = time.time()
    duration = 40  # seconds
    try:
        
        while True:
            wdt.feed()
            '''Unconment only what you want it to do '''
            station = [8,1] # artificially set station position
            #movement  = [forward,left,right]
            nest = [0,0] #coordinate of the nest
        
        
        
            if time.time() - start_time > duration:
                print("10 seconds passed, exiting loop.")
                StopMotor()
                break
    
            detected = wall_detection()
            #print("before detected = ",detected)
            time.sleep(0.2)  # Adjust scan interval as needed
    #         forward(72000)
    #         time.sleep(2)
    #         StopMotor()
    #         time.sleep(2)
            if detected == False:
                backward(72000)  # Move forward
                #time.sleep(2)
                print("detected = ",detected)
                
                #StopMotor()
    #             time.sleep(1)
                
            elif detected == True :#True mean sugbal detected
                
                StopMotor()
                #sleep(1)
                leftback(72000)
                print("detected = ",detected)
                time.sleep(5)
        #forward(72000)  # Move forward
        #time.sleep(2)
        #StopMotor()
        #get_charge([station[0]*math.cos(station[1]),station[0]*math.sin(station[1])])
        #get_charge(nest) #go home


        #rgb.color = (0, 0,100) #red
        # sleep(2)

        # rgb.color = (0, 255, 0) #blue
        #sleep(2)
        #rgb.color = (255,0,0) #green

        #forward(72000)  # Move forward
        #sleep(2)
#         StopMotor()
#         sleep(3)
    except Exception as e:
        print("Error:", e)
        reset()
        
    except KeyboardInterrupt:
        print("KeyboardInterrupt caught. Stopping motor.")
        StopMotor()
        
    finally:
            # 关键清理步骤
            IR_transmitter_pin.duty_u16(0)  # 关闭红外发射
            IR_transmitter_pin2.duty_u16(0)
            IR_transmitter_pin3.duty_u16(0)
            StopMotor()                     # 停止电机
            rgb.color=(0,0,0)                       # 关闭LED
            print("turning off...")
            time.sleep(1)
            sys.exit()
            
    
        
if __name__ == "__main__":
    main()


    # # Gradually colour cycle through colours between red and green, green and blue then blue and red
    # rgb.cycle()a
    # sleep(4)
    # rgb.off()
    # sleep(1)
    # 
    # # Colour cycle slower in the opposite direction
    # rgb.cycle(fade_times=3, colors=((0, 0, 1), (0, 1, 0), (1, 0, 0)), wait=True, n=2)
    # rgb.off()

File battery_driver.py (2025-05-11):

from machine import ADC, Pin
import time


# ADC channels (GPIO26 = ADC0, GPIO27 = ADC1)
supercap_1 = ADC(0)  # Supercapacitor 1
supercap_2 = ADC(1)  # Supercapacitor 2

# Voltage divider scale based on resistors being 68kOhm and 420kOhm
# Example: If you use a 2:1 divider, then battery voltage = adc_voltage * 2
VOLTAGE_DIVIDER_RATIO = 420/68

# ADC reference voltage and resolution
ADC_REF_VOLTAGE = 3.3
ADC_MAX = 65535  # 16-bit resolution on RP2040's ADC in MicroPython

# Shutdown threshold (in volts)
CUTOFF_VOLTAGE = 2.4

# Output pin to disable the OR controller (active low)
enable_pin = Pin(15, Pin.OUT)  

# === FUNCTIONS ===

def read_voltage(adc):
    raw = adc.read_u16()
    voltage = (raw / ADC_MAX) * ADC_REF_VOLTAGE * VOLTAGE_DIVIDER_RATIO
    return voltage

def check_if_power_off_req(supercap_1, supercap_2):
    v_supercap1 = read_voltage(supercap_1)
    v_supercap2 = read_voltage(supercap_2)
    
    print("Battery 1: {:.2f} V | Battery 2: {:.2f} V".format(v_supercap1, v_supercap2))

    if v_supercap1 <= CUTOFF_VOLTAGE or v_supercap2 <= CUTOFF_VOLTAGE:
        print("Supercapacitor voltages below 2.4V! Shutting down OR controller.")
        enable_pin.value(1)  # Disable OR controller (active-low OFF)
    else:
        enable_pin.value(0)  # Enable OR controller (active-low ON)

    time.sleep(1)  # Delay between checks

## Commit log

2025-03-24 Add a file containing navigation algorithms
    Incomplete version still requires
    - obstacle avoidant
    - update position
    - broadcasting position
    - imu implementation for finer movement
2025-04-30 Update test.py
    Change GPIO pins according to the robot PCB.
    Still need to integrate IR and Wall collision.
2025-05-09 Update README.md
    add a software architecture flow chart
2025-05-11 ADC and OR controller driver
    Disables output to the OR controller through its active low input when either of the two supercapacitors reaches a voltage lower than 2.4V
2025-05-11 Rev. A PCB-robot kiCAD files
    Originated in kiCAD 9.0, with generated gerber ffiles, schematic and PCB pdfs
    [bio_robots-B_Courtyard.gbr, bio_robots-B_Cu.gbl, bio_robots-B_Fab.gbr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]
2025-05-15 Update main.py
    Delete ain/bin in. StopMotor()
    Change reset() to sys.exit() for soft reboot instead of hard reboot
    [main.py]
